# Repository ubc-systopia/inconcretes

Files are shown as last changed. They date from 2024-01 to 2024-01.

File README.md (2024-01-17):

<!-- # IVP System Guide -->

This repository contains source code and build documentation for a physical inverted pendulum test platform. The physical system, seen below, works to keep the pendulum shaft upright by actuating a pendulum cart along a track. To achieve this, we use a PID controller program that runs on a network of 4 Raspberry Pis. The Pis are able to communicate with each other using a distributed key value store. 

<p align = "center">
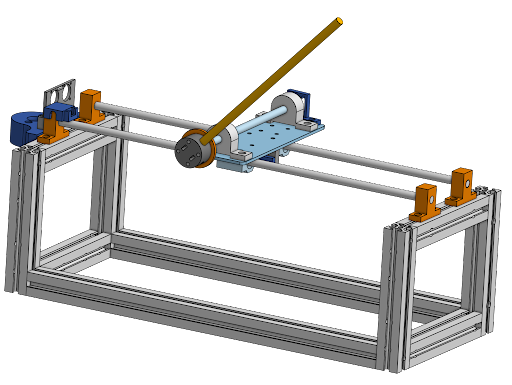
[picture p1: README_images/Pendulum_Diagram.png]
  
</p>

## Controls

### PID Control
<p align="center">
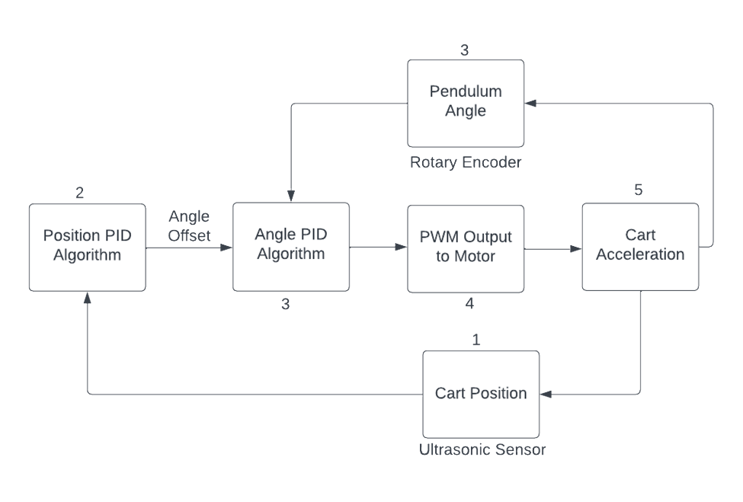
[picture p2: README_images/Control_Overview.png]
  
</p>

PID Control is used to actuate system and balance the pendulum. There are 2 PID algorithms running at different sampling rates (30 Hz for Position PID and 200 Hz for Angle PID were lower bounds in our testing). 

The PID algorithm tracks the error of a system over time and applies the following computation to it:

$$
  u(t)=K_pe(t)+ K_i \int_{a}^{b} e(\tau) \,d\tau + K_d \frac{d}{dt} e(t)
$$
<!-- <p align="center">
  <img src="README_images/PID_Equation.png" />
</p> -->
<!-- ![PID_Equation](README_images/PID_Equatvion.png) -->

The proportional term of $K_pe(t)$ can be thought of as **reacting immediately to the current error**, the integralterm as **accumulating past errors over time**, and the derivative as **predicting future error trends**. PID control offers a cost-effective and straightforward solution compared to more complex control methods. 

The position PID algorithm takes the Cart Position as an input. This is given by an ultrasonic sensors on the sides of the assembly, then filtered before being passed as an input. The position PID algorithm then computes an output which we call an Angle Offset. This is an offset to the real angle of the pendulum and works to amplify the response of the angle controller when the cart nears the edges of the track. Without this controller, the pendulum has no incentive to remain with the bounds of the track.

The angle controller takes the current angle of the pendulum along with the offset provided by the position controller and computes the appropriate signal to send to the motor accordingly. A larger deviation from the desired angle results in more force applied by the motor to correct the pendulum.

## System Overview

### Starting with a Single Node Setup

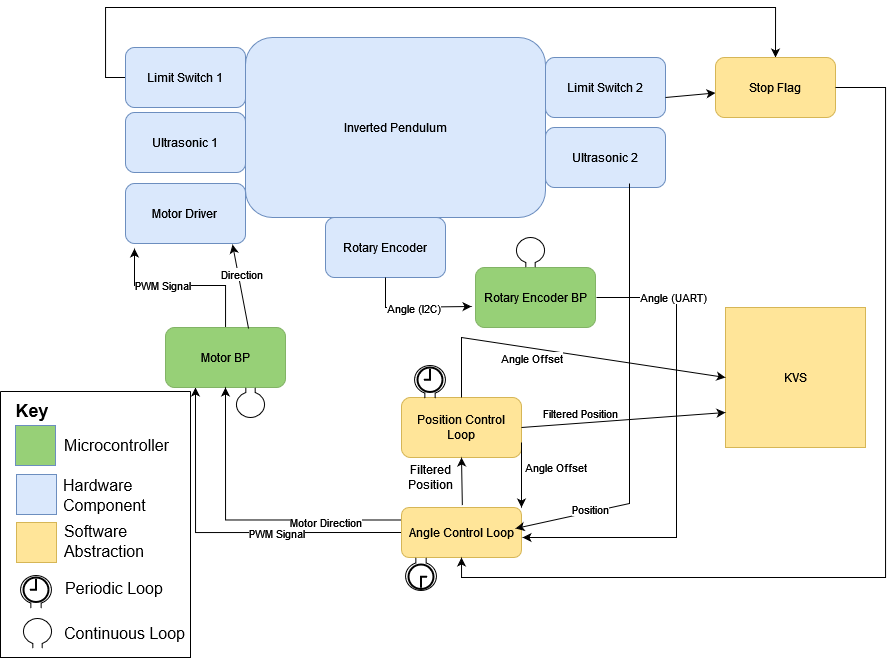
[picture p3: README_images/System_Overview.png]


A diagram for the system for a single node configuration is seen above.  

The physical build consists of the pendulum itself, with a Rotary Encoder, 2 Ultrasonic sensors, 2 limit switches and a motor driver. 

In order to control the pendulum we periodically drive the motor on the pendulum using a PWM signal, which is scaled and given direction based on the state of the system, using the PID scheme outlined above.

The single node in the setup is running 2 periodic tasks at different periods, a **Position Control Loop** and an **Angle Control Loop**. At the Position Control Loop we read a filtered position of the cart and use this as input to the Position PID algorithm. The output is saved to our Key Value Store and is shared with the Angle Control Loop through a shared memory location. 

The **Rotary Encoder BP** is a microcontroller running a continuous loop which reads the **Rotary Encoder** to find the current angle of the pendulum in every loop and forwards this value to the **Angle Control Loop**. The **Angle Control Loop** also receives a reading for the cart's current position along the track from **Ultrasonic 1**. 

 The **Angle Control Loop** performs some filtering of the position and shared this back to the Position Control Loop through a shared memory location. The **Angle Control Loop** uses the output of the position control loop for the angle PID algorithm to give us the output to the Pendulum. This output is in the form a scalar value that is then translated to the duty cycle and direction of a PWM signal.

The **Motor BP** is another microcontroller that is running a continuous loop where it receives the PWM signal from the **Angle Control Loop** and forwards it to the motor driver which then actuates the actual pendulum to achieve control. 

### Moving to a Multi Node Setup

<p align="center">
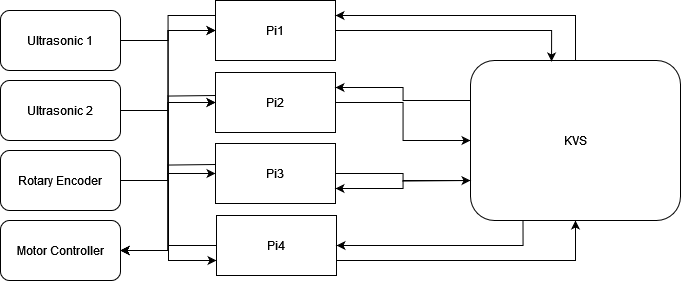
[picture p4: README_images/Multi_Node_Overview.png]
  
</p>
<!-- ![MultiNode.drawio(2).png](README_images/Multi_Node_Overview.png) -->

In a Multi Node Setup,, we have a maximum of 4 Raspberry Pi Nodes. Each of these is running an **Angle Control Loop** and a **Position Control Loop**. 2 Pis are capable of receiving position values from an independent Ultrasonic Sensor, and all 4 Pis are capable of receiving angular values from the **Rotary Encoder BP**. 

Position values can be shared across the Pis using the KVS, along with the control output from each Pi, along with any other values.

Each Pi computes its own control output, comprised of the PWM and Direction signals which are sent to the **Motor BP**. The **Motor BP** is then responsible for deciding on the output to send to the **Motor Driver**, which actuates the cart along the pendulum platform.

## Running on Raspberry Pis

We assume the following:
  - 4 raspberry pi nodes with hostnames `achal01-achal04`
  - nodes can access each other via SSH without passwords
  - this repository is cloned in the home directory of each node
  - PTP is installed
  
### PTP and VLAN config

Run `ifconfig`, expected output:

    eth0: flags=4163<UP,BROADCAST,RUNNING,MULTICAST>  mtu 1500
            inet 198.162.55.144  netmask 255.255.254.0  broadcast 198.162.55.255
            inet6 fe80::3a6:5deb:2c59:cd7f  prefixlen 64  scopeid 0x20<link>
            ether dc:a6:32:cd:ce:77  txqueuelen 1000  (Ethernet)
            RX packets 130046388  bytes 273546776 (260.8 MiB)
            RX errors 0  dropped 0  overruns 0  frame 0
            TX packets 131685298  bytes 406542628 (387.7 MiB)
            TX errors 0  dropped 0 overruns 0  carrier 0  collisions 0

    lo: flags=73<UP,LOOPBACK,RUNNING>  mtu 65536
            inet 127.0.0.1  netmask 255.0.0.0
            inet6 ::1  prefixlen 128  scopeid 0x10<host>
            loop  txqueuelen 1000  (Local Loopback)
            RX packets 76902811  bytes 8946060175 (8.3 GiB)
            RX errors 0  dropped 0  overruns 0  frame 0
            TX packets 76902811  bytes 8946060175 (8.3 GiB)
            TX errors 0  dropped 0 overruns 0  carrier 0  collisions 0

Run the following commands:
  ```bash
    sudo ip link add link eth0 name eth0.11 type vlan id 1 egress 0:2 1:2 2:2 3:2 4:2 5:2 6:2 7:2
    sudo ip link add link eth0 name eth0.12 type vlan id 2 egress 0:4 1:4 2:4 3:4 4:4 5:4 6:4 7:4
  ```
Again run `ifconfig`, expected output:
```
eth0: flags=4163<UP,BROADCAST,RUNNING,MULTICAST>  mtu 1500
        inet 198.162.55.144  netmask 255.255.254.0  broadcast 198.162.55.255
        inet6 fe80::3a6:5deb:2c59:cd7f  prefixlen 64  scopeid 0x20<link>
        ether dc:a6:32:cd:ce:77  txqueuelen 1000  (Ethernet)
        RX packets 130046461  bytes 273556620 (260.8 MiB)
        RX errors 0  dropped 0  overruns 0  frame 0
        TX packets 131685371  bytes 406551468 (387.7 MiB)
        TX errors 0  dropped 0 overruns 0  carrier 0  collisions 0

eth0.11: flags=4163<UP,BROADCAST,RUNNING,MULTICAST>  mtu 1500
        inet6 fe80::6584:daac:a387:87c4  prefixlen 64  scopeid 0x20<link>
        ether dc:a6:32:cd:ce:77  txqueuelen 1000  (Ethernet)
        RX packets 0  bytes 0 (0.0 B)
        RX errors 0  dropped 0  overruns 0  frame 0
        TX packets 4  bytes 686 (686.0 B)
        TX errors 0  dropped 0 overruns 0  carrier 0  collisions 0

eth0.12: flags=4163<UP,BROADCAST,RUNNING,MULTICAST>  mtu 1500
        inet6 fe80::824d:a435:2f9b:ca3a  prefixlen 64  scopeid 0x20<link>
        ether dc:a6:32:cd:ce:77  txqueuelen 1000  (Ethernet)
        RX packets 0  bytes 0 (0.0 B)
        RX errors 0  dropped 0  overruns 0  frame 0
        TX packets 7  bytes 976 (976.0 B)
        TX errors 0  dropped 0 overruns 0  carrier 0  collisions 0

lo: flags=73<UP,LOOPBACK,RUNNING>  mtu 65536
        inet 127.0.0.1  netmask 255.0.0.0
        inet6 ::1  prefixlen 128  scopeid 0x10<host>
        loop  txqueuelen 1000  (Local Loopback)
        RX packets 76902811  bytes 8946060175 (8.3 GiB)
        RX errors 0  dropped 0  overruns 0  frame 0
        TX packets 76902811  bytes 8946060175 (8.3 GiB)
        TX errors 0  dropped 0 overruns 0  carrier 0  collisions 0
```
Check the PTP status using systemctl status ptp4l and find the path of the ptp4l service

For example, the output will contain a line `Loaded: loaded ( ; enabled; vendor preset: enabled)`

Open file using  `sudo vim /lib/systemd/system/ptp4l.service` and check the ethernet interface used by PTP

By default, it is `eth0`, replace it with `eth0.11`

Run the following systemctl commands:
  ```bash
  sudo systemctl daemon-reload
  sudo systemctl restart ptp4l
  ```

### Running the Pendulum
<!-- 1. Run [`setup.sh`](http://setup.sh) on each Pi -->
1. Naviagate to this repository on Pi 1
2. Build the project:
    1. Navigate to the `build` directory
    2. run `cmake ..`
    3. run `make`
3. Enable UART on each of the Pis from the `raspi config` tool.
4. Callibrate pendulum by running the following command in the build directory of any of the connected Pis:
    ``` bash
    sudo ./test_AS5600
    ```
    This displays the rotary encoder angle, balance the pendulum manually and note the encoder value shown in the terminal. Ideally, this should be 2000 plus or minus 300, to keep the rollover state for angle outside the operating range of the pendulum.

5. Run the pendulum application from the project directory:

    ```bash
    sudo ./pivp_run.sh $NUM_NODES $POSITION_LOOP_PERIOD $ANGLE_LOOP_PERIOD $POSITION_KP $POSITION_KD $POSITION_KI $ANGLE_KP $ANGLE_KD $ANGLE_KI $POSITION_SET_POINT $ANGLE_SET_POINT
    ```

      Values that worked well for our system for the other parameters:

      | Parameter | Value |
      |--- | --- |
      |`NUM_NODES`| number of nodes you are running with| 
      | `POSITION_LOOP_PERIOD`: | 20 |
      | `ANGLE_LOOP_PERIOD`: | 6 |
      | `POSITION_KP`: | 0.01 |
      | `POSITION_KD`: | 0.08 |
      | `POSITION_KI`: | 0 |
      | `ANGLE_KP`: | 25 |
      | `ANGLE_KD`: | 2.5 |
      | `ANGLE_KI`: | 150 |
      | `POSITION_SET_POINT`: | 20 - Corresponds to distance from side to middle of track in cm |
      | `ANGLE_SET_POINT`: | calibration value from previous step |

6. Press either limit switch on sides of pendulum track to stop a run of the pendulum
7. Logs for the run are available at local nodes at ‘PiCtlLogs/date-of-runcompletion_time-of-completion_PiN’

## Pendulum Build Documentation
Detailled descriptions of how to build the pendulum and various aspects of the systemn are included in subdirectories of this project.
- [`Bluepill_Firmware`](Bluepill_Firmware): Firmware for 2 Bluepill microcontrollers used, along with instructions for how to flash the firmware on the devices.
- [`PCB_Designs_Docs`](PCB_Designs_Docs): All PCB design files for the custom PCBs used in the pendulum, including labelled circuit diagrams for reference, gerber and drill files for fabrication. Additionally, all electrical components and quantities, with purchase links are shown. 
- [`Mech_Docs`](Mech_Docs): All mechanical components with purchase links and quantities are included. Additionally, CAD design files, STL files for 3D printed parts and DXFs for laser cut parts are included.

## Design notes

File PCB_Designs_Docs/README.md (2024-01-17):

# Inverted Pendulum Electrical Documentation and PCB Designs

## Components/Sensors Used

| Component | Quantity | Purchase Link | Notes |
| --- | --- | --- | --- |
| Ultrasonic Sensor | 2 | https://www.digikey.ca/short/wqjn48db |  |
| AS5600 Rotary Encoder | 1 | https://a.co/d/2jkT8j0 | Prebuilt breakout board with magnet included used |
| Brushed DC Motor | 1 | https://a.co/d/41Gn3cl | Any smooth motion motor with low cogging and similar specifications is usable. |
| Raspberry Pi 4B | 4 | -  | - |
| Bluepill (STM32F103C dev board) | 2 | https://a.co/d/aVWNCsf |  |
| ST-Link V2 | 1 | https://a.co/d/aVWNCsf |  |
| 12 V Motor Driver | 1 | https://www.cytron.io/p-10amp-5v-30v-dc-motor-driver |  |
| 12 V Power Supply | 1 | https://www.digikey.ca/short/t58bfrvt |  |
|  4.7 kOhm Resistor | 2 | https://www.digikey.ca/short/v238crf2 | For I2C Lines |
| JST Connector Set | 1 | https://a.co/d/0fB4Xf2 |  |
| I2C OLED Display Module | 2 | https://a.co/d/eMWrLmH |  |
| Header Pins (Male) | 8 | https://www.digikey.ca/short/54wwz4hv |  |
| Header Pins (Female) | 4 | https://www.digikey.ca/short/5cdf2dd4 |  |
| Custom PCBs | 4 | Download design files and manufacture at any PCB fab. | Details included below in PCB Design Section |
| PJ002A Connector | 1 | https://www.digikey.ca/short/v80h319m |  |
| AC DC Wall Power Adapter, Barrel Jack | 1 | https://www.digikey.ca/short/rw25c3v4 |  |
| Limit Switch | 2 | https://www.digikey.ca/short/8dmrj95d |  |

## PCB Design

In testing and integration of the system, I found that wiring using Dupont (jumper) wires to connect to the Pi headers was not a suitable long term solution as sensors would come unplugged and connections were unreliable. 

I elected to instead design a few custom Pi Hat PCBs that could plug into the Raspberry Pi 4Bs GPIO Headers. These PCBs included JST connectors for more permanent connections to sensors and allowed for cleaner, reliable wiring. To keep connections clean, zip ties and cable tie mounts were used to bundle and route wires.

Below are descriptions for the KiCad projects used to manufacture the PCBs for the project, as well as labelled diagrams of the PCB for an end user.

### **PCB Files**

Pi Hat (`Pi1_PiHat`):

This is the Pi Hat for the “main” Raspberry Pi. In a single node setup, this PCB alone with 1 Raspberry PI is sufficient. 

<p align="center">
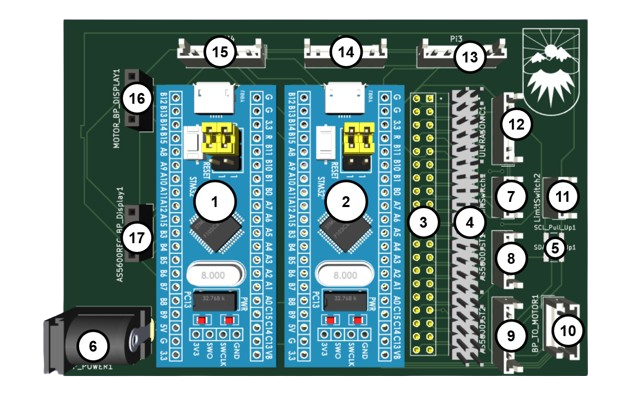
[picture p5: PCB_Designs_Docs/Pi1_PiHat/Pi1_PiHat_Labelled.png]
  
</p>

<!-- ![Pi1_PiHat_Labelled.png](./Pi1_PiHat/Pi1_PiHat_Labelled.png) -->

| Number | Label | Description |
| --- | --- | --- |
| 1 | AS5600 Distributor Bluepill | BP responsible for receiving AS5600 communication over I2C and sending this over UART to all connected Pis |
| 2 | PWM Forwarder Bluepill | BP responsible for receiving the PWM signal from all Pi’s and sending the final output PWM signal to the motor |
| 3 | Board to Pi Header | Connects to 40 pin Pi Header |
| 4 | Pi Header Extension | Allows access to all Pi Header pins |
| 5 | I2C Pullup Resistors |  |
| 6 | Barrel Jack (PJ002A) | 3V3 Power Input for Bluepills |
| 7 | Limit Switch 1 Connector | Limit switch input, allows detection for when cart is at rails of the physical track |
| 8 | AS5600 Connector 1 | Connector for I2C comms, direction signal and programming pins of AS5600 |
| 9 | AS5600 Connector 2 | Connector for power, ground and analog output of AS5600 |
| 10 | BP to Motor Connector | Connection to share ground, send direction and PWM to the motor driver |
| 11 | Limit Switch 2 Connector | Limit switch input, allows detection for when cart is at rails of the physical track |
| 12 | Ultrasonic 1 Connector |  |
| 13 | Pi1 to Pi3 Connector | Connects ground, AS5600 Distributor BP UART Tx line, limit switches and motor instruction lines |
| 14 | Pi1 to Pi2 Connector | Connects ground, AS5600 Distributor BP UART Tx line, limit switches and motor instruction lines |
| 15 | Pi1 to Pi4 Connector | Connects ground, AS5600 Distributor BP UART Tx line, limit switches and motor instruction lines |
| 16 | PWM Forwarder BP to Display Connector | Connector for BP to digital display |
| 17 | AS5600 Distributor BP to Display Connector | Connector for BP to digital display |

Pi Hat 2 (`Pi2_PiHat`):

This is the Pi Hat for the secondary node for a simple two node setup. The second node has a connector to the “main” Pi Hat as well as an additional Ultrasonic sensor.

<p align="center">
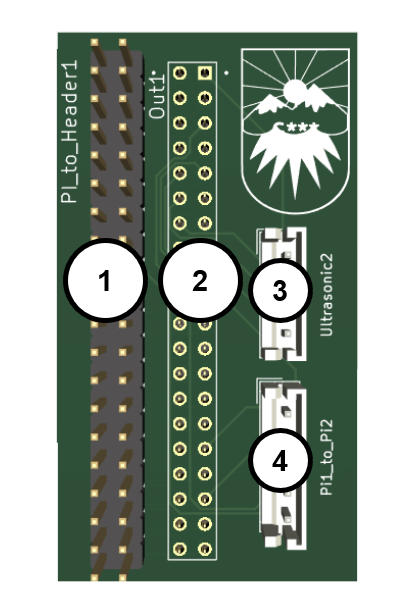
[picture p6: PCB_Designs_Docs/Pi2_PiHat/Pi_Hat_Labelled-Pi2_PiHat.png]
  
</p>

| Number | Label | Description |
| --- | --- | --- |
| 1 | Board to Pi Header | Connects to 40 pin Pi Header |
| 2 | Pi Header Extension | Allows access to all Pi Header pins |
| 3 | Ultrasonic 2 Connector |  |
| 4 | Pi1 to Pi2 Connector | Connects ground, AS5600 Distributor BP UART Tx line, limit switches and motor instruction lines |

Pi Hat N (`PiN_PiHat`):
<p align="center">
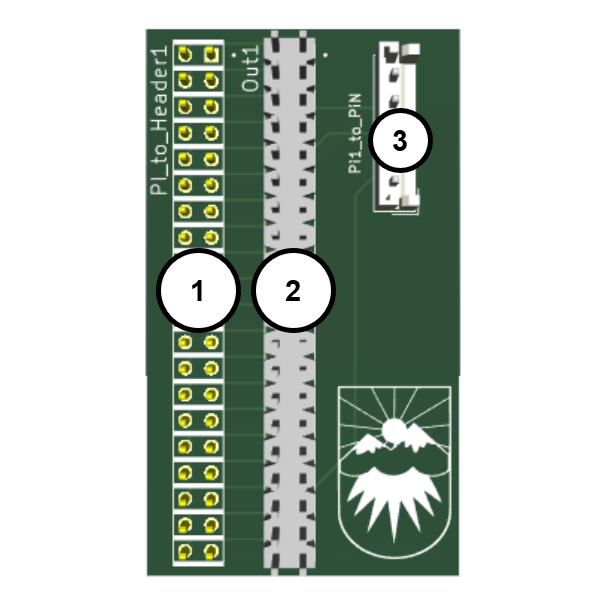
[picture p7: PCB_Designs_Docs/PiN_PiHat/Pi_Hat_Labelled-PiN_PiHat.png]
  
</p>

| Number | Label | Description |
| --- | --- | --- |
| 1 | Board to Pi Header | Connects to 40 pin Pi Header |
| 2 | Pi Header Extension | Allows access to all Pi Header pins |
| 4 | Pi1 to PiN Connector | Connects ground, AS5600 Distributor BP UART Tx line, limit switches and motor instruction lines |

This is the Pi Hat for all additional nodes. It includes a connector to the main Pi Hat to share ground, a UART line, limit switch input, and outputs to the motor driving Bluepill.

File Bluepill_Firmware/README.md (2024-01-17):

# Inverted Pendulum Firmware

### Microcontroller Firmware

The microcontroller chosen for this project was the STM32F103C, commonly use as part of the dev board known as the Bluepill:

<!-- ![Untitled](README_images/Bluepill.jpeg) -->
<p align="center">
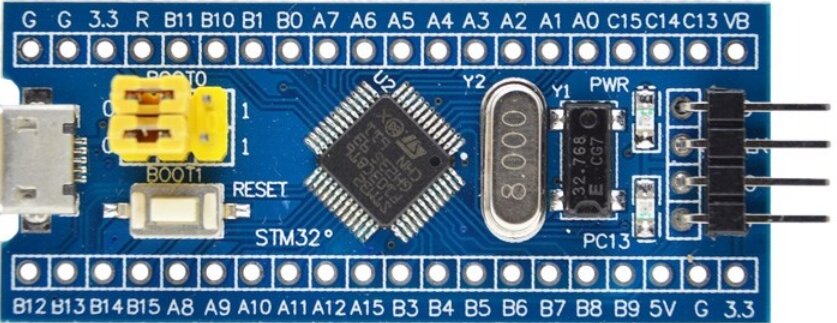
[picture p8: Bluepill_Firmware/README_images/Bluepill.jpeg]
  
</p>

To allow the Raspberry Pi nodes for the Inverted Pendulum to act as replicas in a distributed system, we did not want to have leader nodes. In order to actuate the motor for the pendulum, we need a single input to a motor driver circuit in the form of a PWM signal. So, we elected to use an intermediate microcontroller which is responsible for receiving the output in the form of a PWM signal from all of the Raspberry Pi nodes, and then output a final PWM signal to the motor driver.

<p align="center">
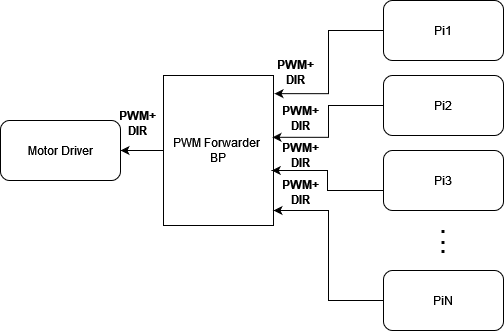
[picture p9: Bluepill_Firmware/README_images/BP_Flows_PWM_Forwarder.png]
  
</p>
<!-- ![BP_Flows_PWM_Forwarder.png](README_images/BP_Flows-PWM_Forwarder.png) -->

A second Bluepill is used to distribute the rotary encoder output to the Raspberry Pi nodes. This Bluepill acts as an I2C master to the AS5600 I2C minion rotary encoder. The received angle is then sent to the raspberry pi nodes over UART as the Raspberry Pi 4B used for this project does not have the necessary hardware to be used as an I2C minion. 

<p align="center">
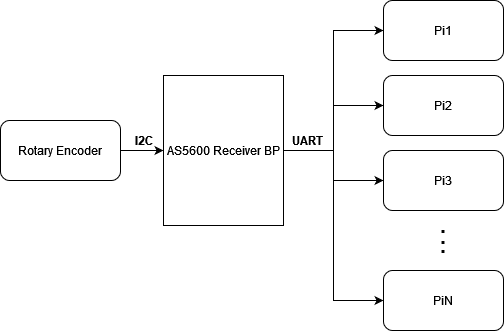
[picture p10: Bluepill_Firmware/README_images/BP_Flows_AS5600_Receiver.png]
  
</p>
<!-- ![BluepillFlows.drawio.png](README_images/BP_Flows_AS5600_Receiver.png) -->

For ease of development and flashing, we elected to use PlatformIO with the Arduino framework for the firmware on the microcontrollers. PlatformIO is an open-source ecosystem for embedded development that provides a unified development platform for multiple microcontroller architecture. If you use VSCode, you can install the [PlatformIO extension](https://marketplace.visualstudio.com/items?itemName=platformio.platformio-ide). Otherwise, please install the CLI version, following these instructions:

[https://docs.platformio.org/en/latest/core/installation/index.html](https://docs.platformio.org/en/latest/core/installation/index.html).

The following instructions outline how to flash the Bluepill microcontrollers assuming that you are using the CLI:

Connect to the PWM forwarder Bluepill using an ST-Link V2 programmer. Navigate to ‘BluepillFirmware/PWMForwarder’ in your terminal and run:

```bash
pio run --target upload
```

If flashing is successful and there is no PWM output any connected Pis, the digital display connected to the PWM Forwarder will display “”.

Now, you can connect the ST-Link to the AS5600 Bluepill, navigate to the ‘BluepillFirmware/AS5600ReceiverBP’ folder and run

```bash
pio run --target upload
```

If flashing is successful, and the connection to the sensor is live, then the connected digital display will read “Hello World”.

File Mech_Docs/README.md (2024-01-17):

# Inverted Pendulum Mechanical Design and Build Notes

## Components Used

********Basic components such as nuts, bolts, washers and spacers are not included********

### Pendulum Frame

| Item | Quantity | Link | Specifications |
| --- | --- | --- | --- |
| T-Slot Nuts | 32 | https://www.mcmaster.com/products/t-slot-nuts/t-slotted-framing-fasteners-4/system-of-measurement~metric/rail-height~20mm/ | Single Nut, 20 mm single rail height |
| Corner Brackets | 8 | https://www.mcmaster.com/products/corner-brackets/t-slotted-framing-structural-brackets/ | 20 mm rail height |
| Aluminum T-Slot Framing Rails | 8 | https://www.mcmaster.com/products/aluminum-extrusions/rail-profile~single/single-rail-profile-style~four-slot/system-of-measurement~metric/rail-height~20mm/rail-widt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 | 0.5ft length, 20 mm rail height |
| Aluminum T-Slot Framing Rails | 2 | https://www.mcmaster.com/products/aluminum-extrusions/rail-profile~single/single-rail-profile-style~four-slot/system-of-measurement~metric/rail-height~20mm/rail-widt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 | 1.5 ft length, 20 mm rail height |

### Linear Motion System

| Item | Quantity | Link | Specifications |
| --- | --- | --- | --- |
| Linear Motion Shaft | 2 | https://www.mcmaster.com/products/linear-shafts/linear-motion-shafts-5/system-of-measurement~metric/diameter~8mm/length~600-mm/ | Shaft Length: 8 mm, Shaft Diameter: 600 mm |
| Shaft Collars | 4 | https://www.amazon.ca/Aluminum-Linear-Support-Motion-Diameter/dp/B08JTPG54L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,aps,131&sr=8-2 | Bore Diameter: 8 mm  |
| Linear Ball Bearings | 2 |  | Bore Diameter: 8 mm |
| GT2 Idler | 1 | https://a.co/d/6dsKSIS | Tooth Profile: GT2 |
| GT2 Motor Mounted Pulley | 1 | https://a.co/d/6dsKSIS | Tooth Profile: GT2, Bore Diameter:  |
| Timing Belt | 1 | https://a.co/d/6dsKSIS | Tooth Profile: GT2, Bore Diameter:  |
| Clamp Mount Block | 1 | https://a.co/d/6dsKSIS | Tooth Profile: GT2 |
| Motor Mount | 1 | 3D Print STL: [`Motor_Mount.stl`](Motor_Mount.stl) | Material: PLA, Dimensions: |
| Cart Timing Belt Mount | 1 | 3D Print STL: [Cart_Timing_Belt_Mount.stl](Cart_Timing_Belt_Mount.stl) | Material: PLA, Dimensions: |
| Idler Mount | 1 | 3D Print STL: [`Idler_Mount.stl`](Idler_Mount.stl)  | Material: PLA, Dimensions: |
| Motor Driver Mount | 1 | Laser Cutter DXF: [`Motor_Driver_Mount.stl`](Motor_Driver_Mount.stl) | Material: MDF, Dimensions: |

### **Pendulum Shaft System**

| Item | Quantity | Link | Specifications |
| --- | --- | --- | --- |
| Pendulum to Rotary Shaft Mount | 1 | 3D Print STL: [`Pendulum_To_Rotary_Shaft_Mount.stl`](Pendulum_To_Rotary_Shaft_Mount.stl) | Material: PLA, Dimensions:  |
| Rotary Shaft Flange | 1 | https://a.co/d/g265dLN | Bore Diameter: 10 mm |
| Rotary Mounted Bearings | 1 | https://a.co/d/airvwwv | Bore Diameter: 10 mm |
| Rotary Shaft | 1 | https://www.mcmaster.com/products/rotary-shafts/rotary-shafts-5/system-of-measurement~metric/ | Diameter: 10 mm, Length: 200 mm, Material: 1566 Carbon Steel |
| AS5600 Mount | 1 | 3D Print STL: [`AS5600_Mount.stl`](AS5600_Mount.stl) | Material: PLA, Dimensions:  |
| Pendulum Cart | 1 | Laser Cutter DXF: [`Pendulum_Cart.dxf`](Pendulum_Cart.dxf) | Material: MDF, Dimensions |
|  |  |  |  |

### **Sensor Mounts**

| Item | Quantity | Link | Specifications |
| --- | --- | --- | --- |
| Motor-Side Ultrasonic Mount | 1 | 3D Print STL: [`Ultrasonic_Mount.stl`](Ultrasonic_Mount.stl) | Material: PLA, Dimensions: |
| Idler-Side Ultrasonic Mount | 1 | 3D Print STL: [`TODO`]() | Material: PLA, Dimensions: |
| Limit Switch Mount | 1 | 3D Print STL: [`Limit_Switch_Mount.stl`](Limit_Switch_Mount.stl) | Material: PLA, Dimensions: |
| Ultrasonic Reflection Surface | 1 | Laser Cutter DXF: [`TODO`]() | Material: Cardboard, Dimensions: |

### CAD Files

**Full Assembly**

[Onshape](https://cad.onshape.com/documents/4bf8413ba8de0c065cd15fe9/w/5f5a90b8a1e2c8779d00a033/e/c47179ad8bca38d01a648ef1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)

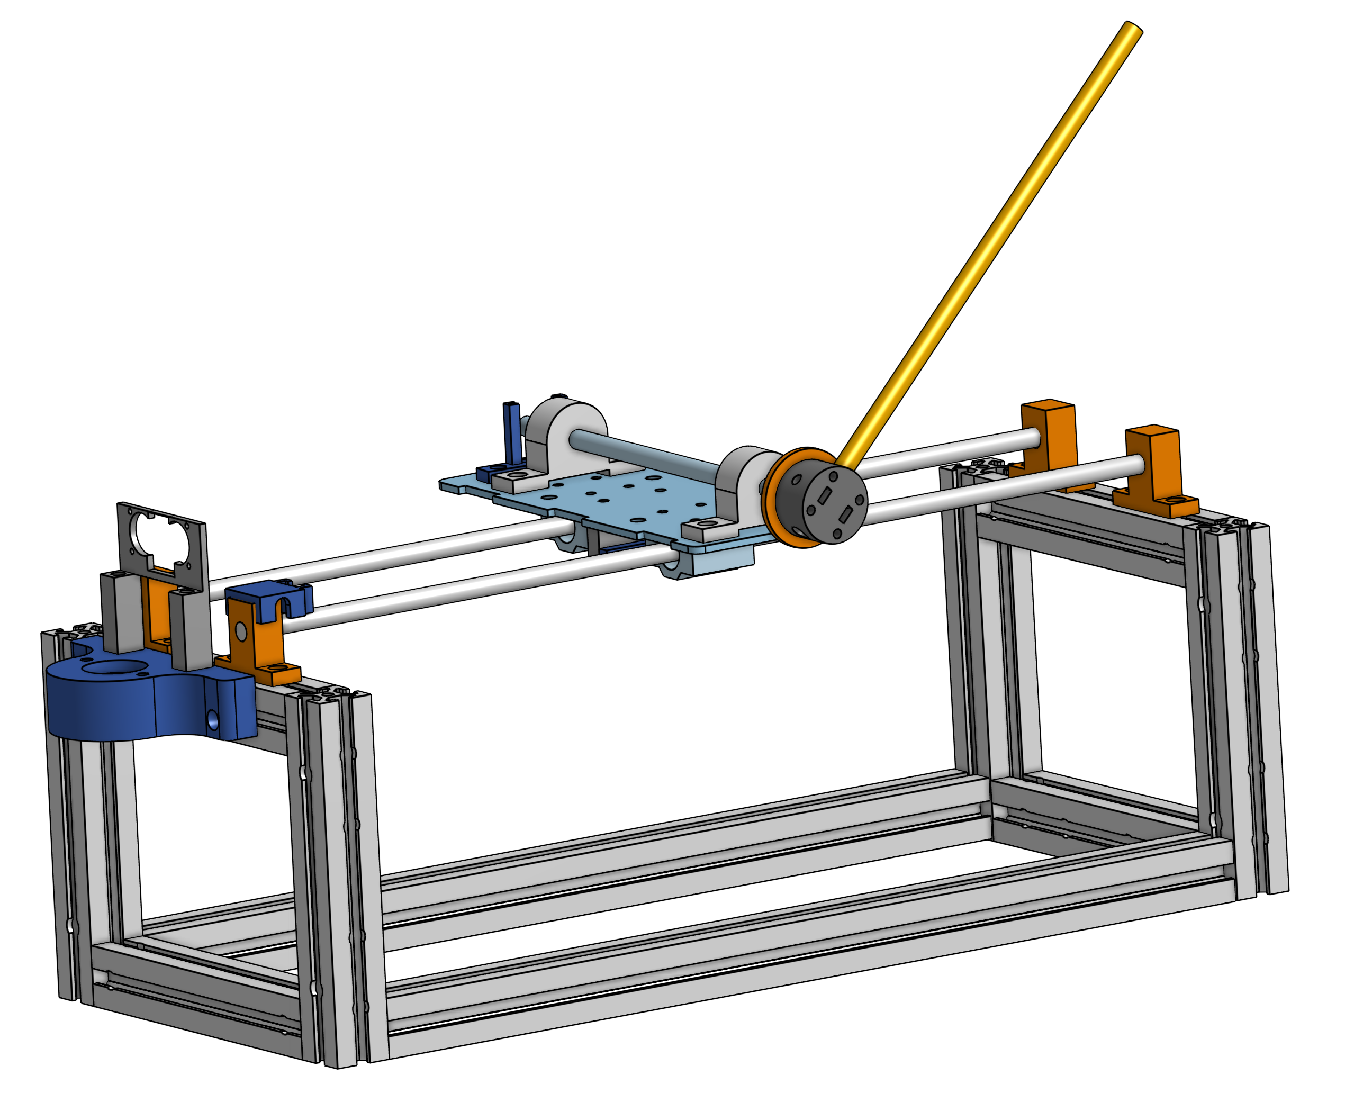
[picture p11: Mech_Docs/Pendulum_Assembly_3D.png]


### Mechanical Build Notes

- Alignment of the linear motion system is a key consideration during construction. Assembly should be completed on a strong, stable and level surface. Movement of the cart along linear motion rails should not cause binding towards the ends of the track, so adjust shaft collar positions along the t-slots as required for smooth motion and aligned linear motion shafts. Smooth motion of this system is important as jolts/jerkiness of the system causes unneeded difficulty in control of the unstable system and misalignments causes reliability concerns.
- Timing Belt should be under appropriate tension, you should be able to “strum” it, like a tight guitar string and it should not hang slack. Tension should be comparable to 3D printer timing belts.
- With the cart in constant motion with changing directions and vibrations in the system, it’s advisable to tighten bolts and add a second locking bolt. Alternatively, components such as loc-tite or locking nuts can be used to reduce the likelihood of vibrations causing nuts to fall.
- The linked aluminium extrusions available on McMaster-Carr have a non-standard footprint (i.e. not the commonly available 80x20 footprint). I would recommend using 8020 extrusions instead as it is easier to find parts to work with these extrusions (i.e. corner gussets, slot nuts, etc.) as you are not limited by what is available on McMaster-Carr. This may also result in a cheaper build.

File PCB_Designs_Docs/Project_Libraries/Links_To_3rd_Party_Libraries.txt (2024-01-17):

20x2 pin male header: https://www.snapeda.com/parts/7-146256-0/TE%20Connectivity/view-part/
Resistors: https://www.snapeda.com/parts/RC1206JR-130RL/Yageo/view-part/
Barrel Jack Power Connector: https://www.snapeda.com/parts/PJ-002A/CUI+Devices/view-part/
20x2 pin female header: https://www.snapeda.com/parts/SSQ-120-01-L-D/Samtec/view-part/

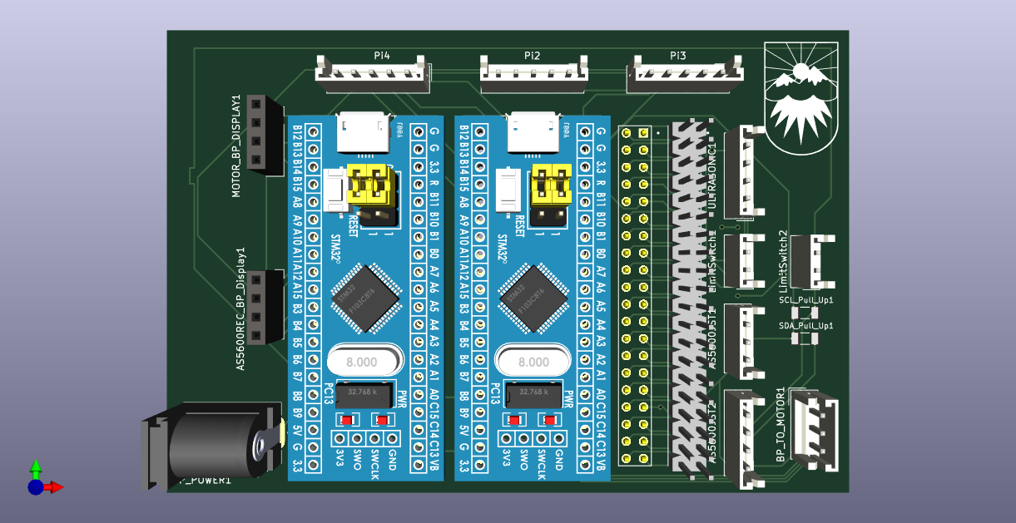
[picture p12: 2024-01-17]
PCB_Designs_Docs/Pi1_PiHat/Pi1_PiHat.png

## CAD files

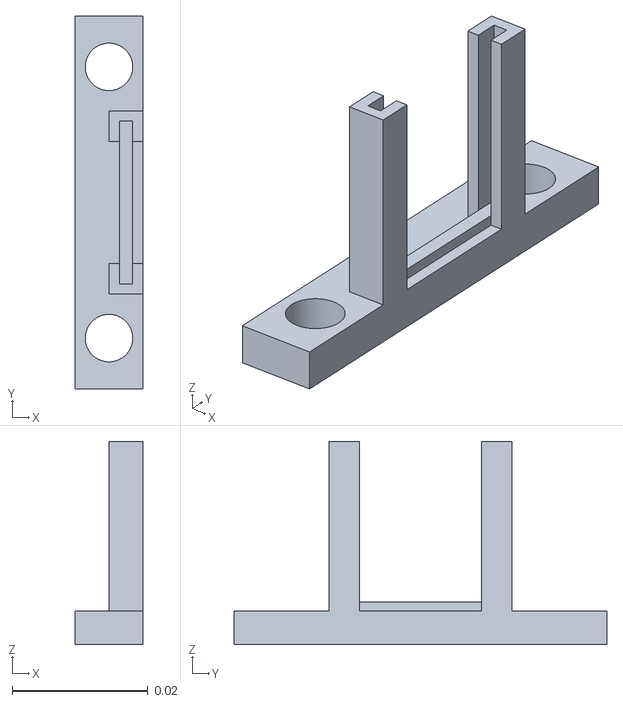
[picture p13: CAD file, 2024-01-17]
Mech_Docs/AS5600_Mount.stl
0.01 x 0.055 x 0.03

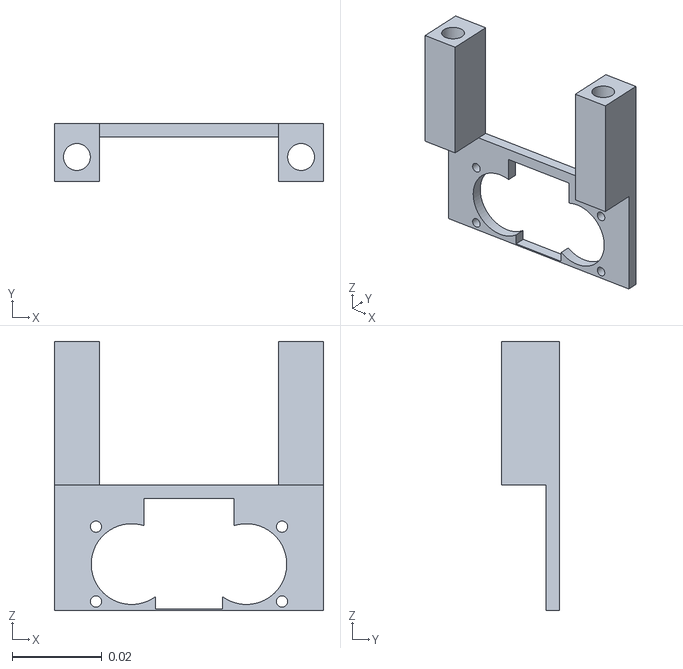
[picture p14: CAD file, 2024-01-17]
Mech_Docs/Ultrasonic_Mount.stl
0.06 x 0.013 x 0.06

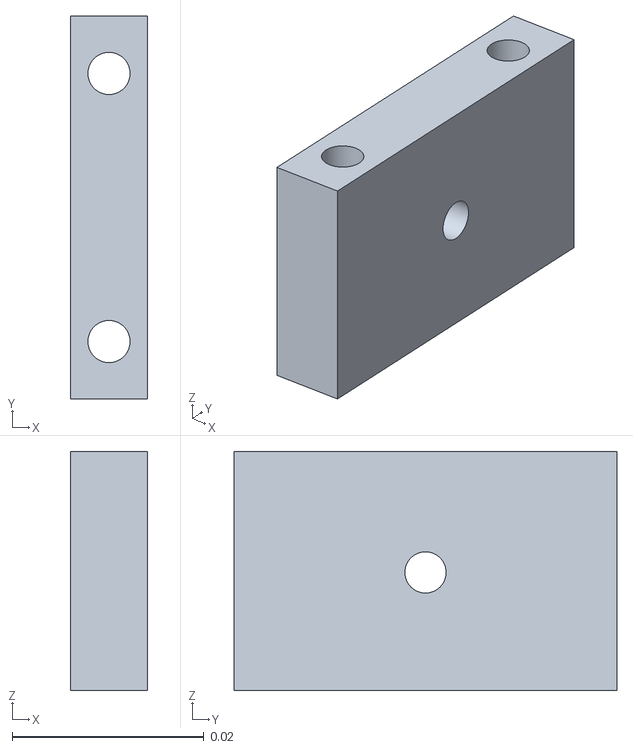
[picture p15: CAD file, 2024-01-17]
Mech_Docs/Cart_Timing_Belt_Mount.stl
0.008 x 0.04 x 0.025

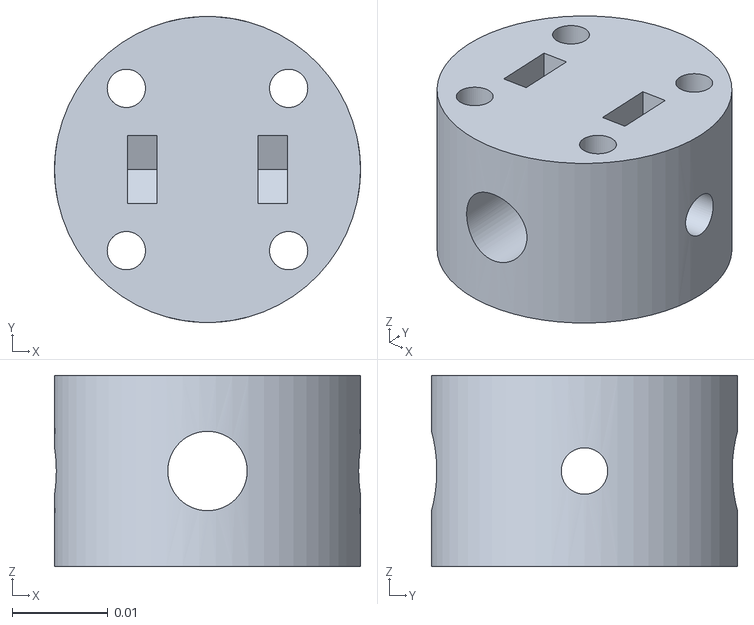
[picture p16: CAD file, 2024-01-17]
Mech_Docs/Pendulum_To_Rotary_Shaft_Mount.stl
0.032 x 0.032 x 0.02

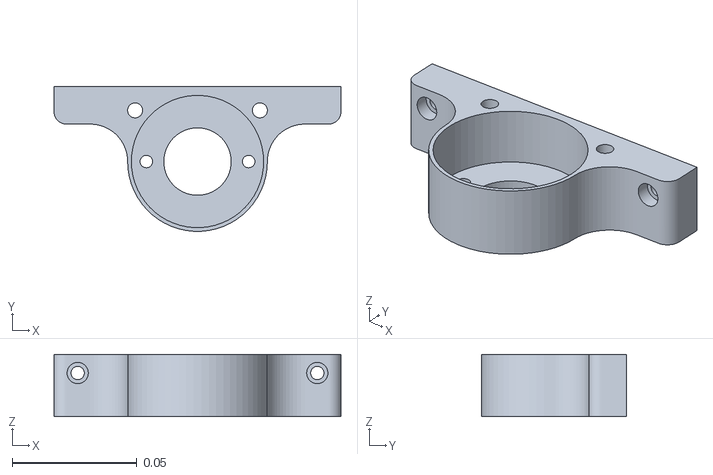
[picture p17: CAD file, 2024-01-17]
Mech_Docs/Motor_Mount.stl
0.115 x 0.058 x 0.025

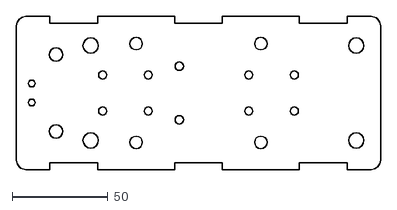
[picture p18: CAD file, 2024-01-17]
Mech_Docs/Pendulum_Cart.dxf
190.0 x 80.0

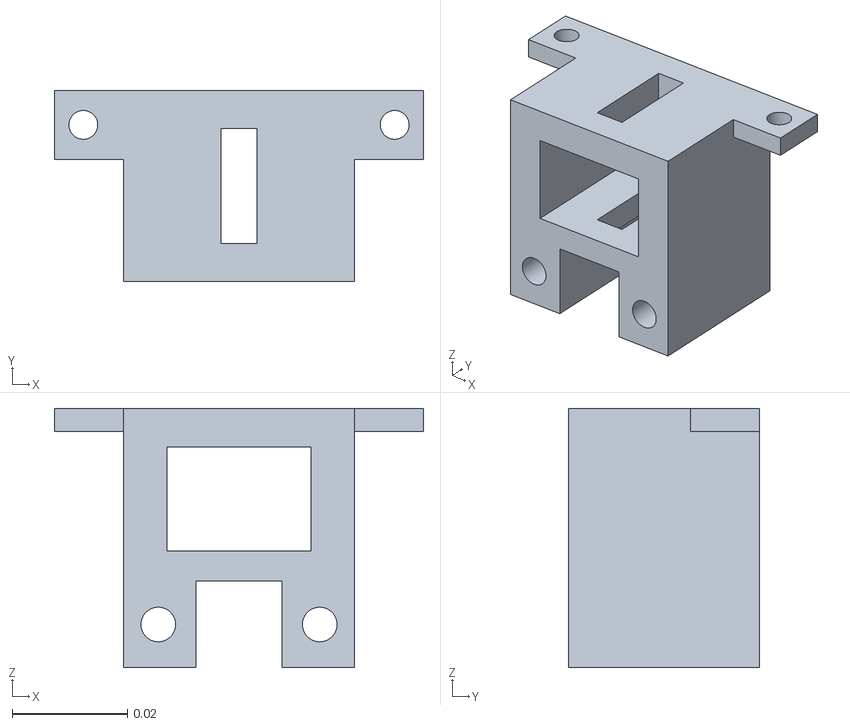
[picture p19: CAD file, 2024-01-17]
Mech_Docs/Idler_Mount.stl
0.064 x 0.0332 x 0.045

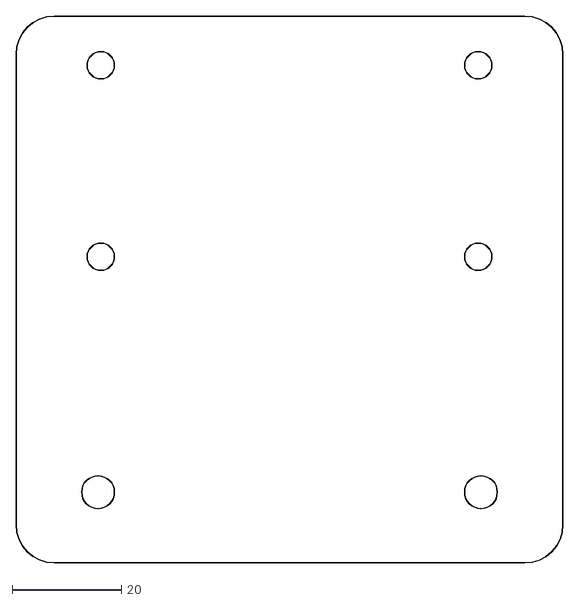
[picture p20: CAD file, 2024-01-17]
Mech_Docs/Motor_Driver_Mount.dxf
100.0 x 100.0

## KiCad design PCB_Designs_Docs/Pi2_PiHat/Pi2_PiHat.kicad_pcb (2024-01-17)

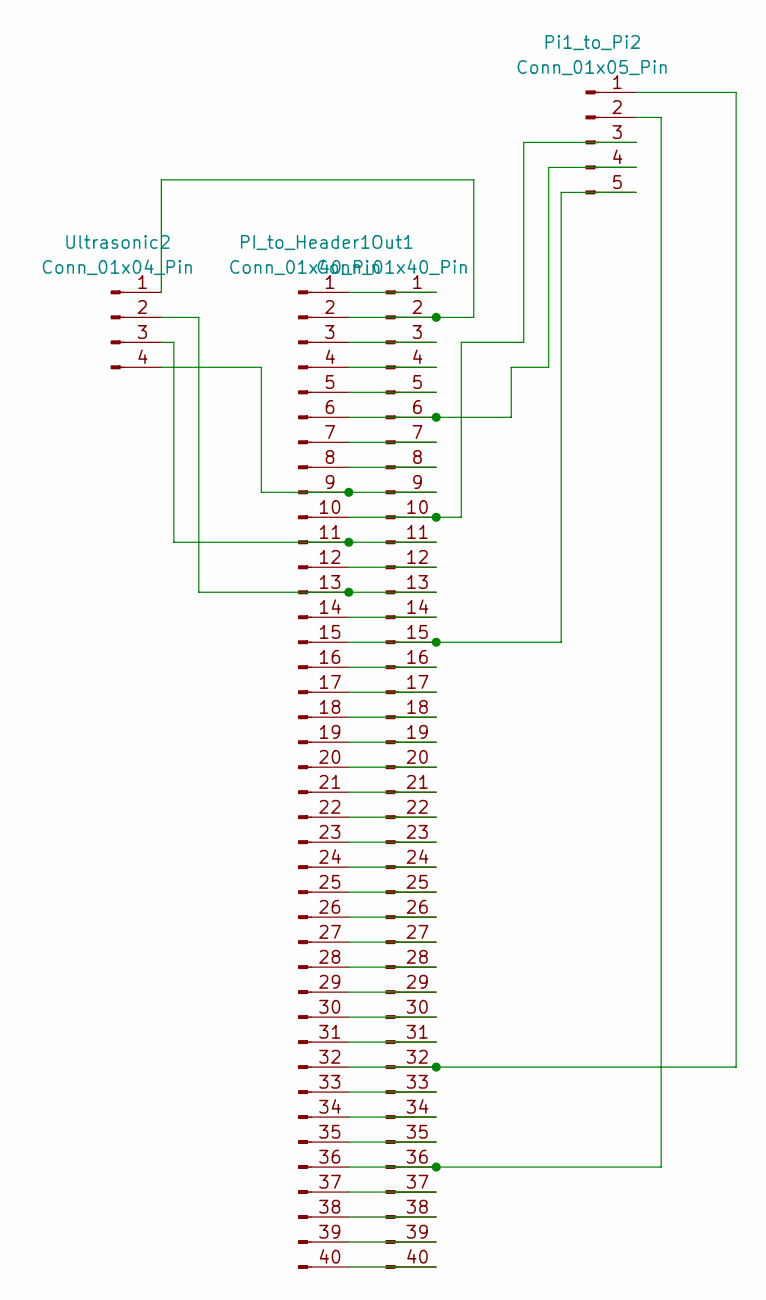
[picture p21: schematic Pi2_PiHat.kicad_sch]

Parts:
Out1: Conn_01x40_Pin; TE_7-146256-0
PI_to_Header1: Conn_01x40_Pin; TE_7-146256-0
Pi1_to_Pi2: Conn_01x05_Pin; JST_EH_B5B-EH-A_1x05_P2.50mm_Vertical
Ultrasonic2: Conn_01x04_Pin; JST_EH_B4B-EH-A_1x04_P2.50mm_Vertical

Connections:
unnamed: Out1.1, PI_to_Header1.1
unnamed: Out1.2, PI_to_Header1.2, Ultrasonic2.1
unnamed: Out1.3, PI_to_Header1.3
unnamed: Out1.4, PI_to_Header1.4
unnamed: Out1.5, PI_to_Header1.5
unnamed: Out1.6, PI_to_Header1.6, Pi1_to_Pi2.4
unnamed: Out1.7, PI_to_Header1.7
unnamed: Out1.8, PI_to_Header1.8
unnamed: Out1.9, PI_to_Header1.9, Ultrasonic2.4
unnamed: Out1.10, PI_to_Header1.10, Pi1_to_Pi2.3
unnamed: Out1.11, PI_to_Header1.11, Ultrasonic2.3
unnamed: Out1.12, PI_to_Header1.12
unnamed: Out1.13, PI_to_Header1.13, Ultrasonic2.2
unnamed: Out1.14, PI_to_Header1.14
unnamed: Out1.15, PI_to_Header1.15, Pi1_to_Pi2.5
unnamed: Out1.16, PI_to_Header1.16
unnamed: Out1.17, PI_to_Header1.17
unnamed: Out1.18, PI_to_Header1.18
unnamed: Out1.19, PI_to_Header1.19
unnamed: Out1.20, PI_to_Header1.20
unnamed: Out1.21, PI_to_Header1.21
unnamed: Out1.22, PI_to_Header1.22
unnamed: Out1.23, PI_to_Header1.23
unnamed: Out1.24, PI_to_Header1.24
unnamed: Out1.25, PI_to_Header1.25
unnamed: Out1.26, PI_to_Header1.26
unnamed: Out1.27, PI_to_Header1.27
unnamed: Out1.28, PI_to_Header1.28
unnamed: Out1.29, PI_to_Header1.29
unnamed: Out1.30, PI_to_Header1.30
unnamed: Out1.31, PI_to_Header1.31
unnamed: Out1.32, PI_to_Header1.32, Pi1_to_Pi2.1
unnamed: Out1.33, PI_to_Header1.33
unnamed: Out1.34, PI_to_Header1.34
unnamed: Out1.35, PI_to_Header1.35
unnamed: Out1.36, PI_to_Header1.36, Pi1_to_Pi2.2
unnamed: Out1.37, PI_to_Header1.37
unnamed: Out1.38, PI_to_Header1.38
unnamed: Out1.39, PI_to_Header1.39
unnamed: Out1.40, PI_to_Header1.40

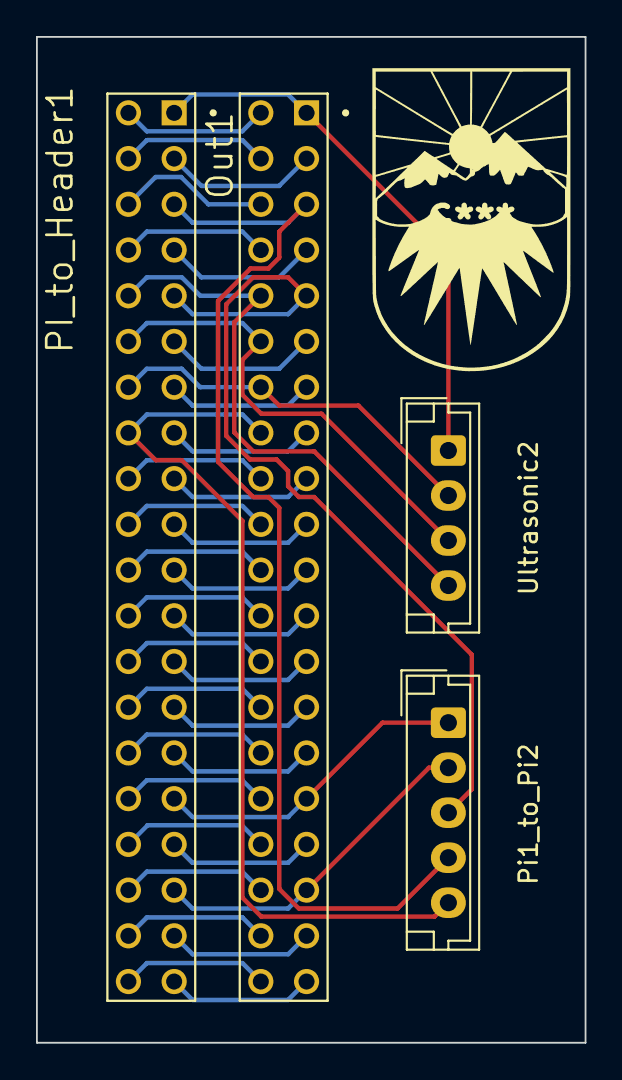
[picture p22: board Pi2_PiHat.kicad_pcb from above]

Board: 2 copper layers, 30.5 x 55.9 mm, 4 parts (0 on the bottom side), 40 nets.

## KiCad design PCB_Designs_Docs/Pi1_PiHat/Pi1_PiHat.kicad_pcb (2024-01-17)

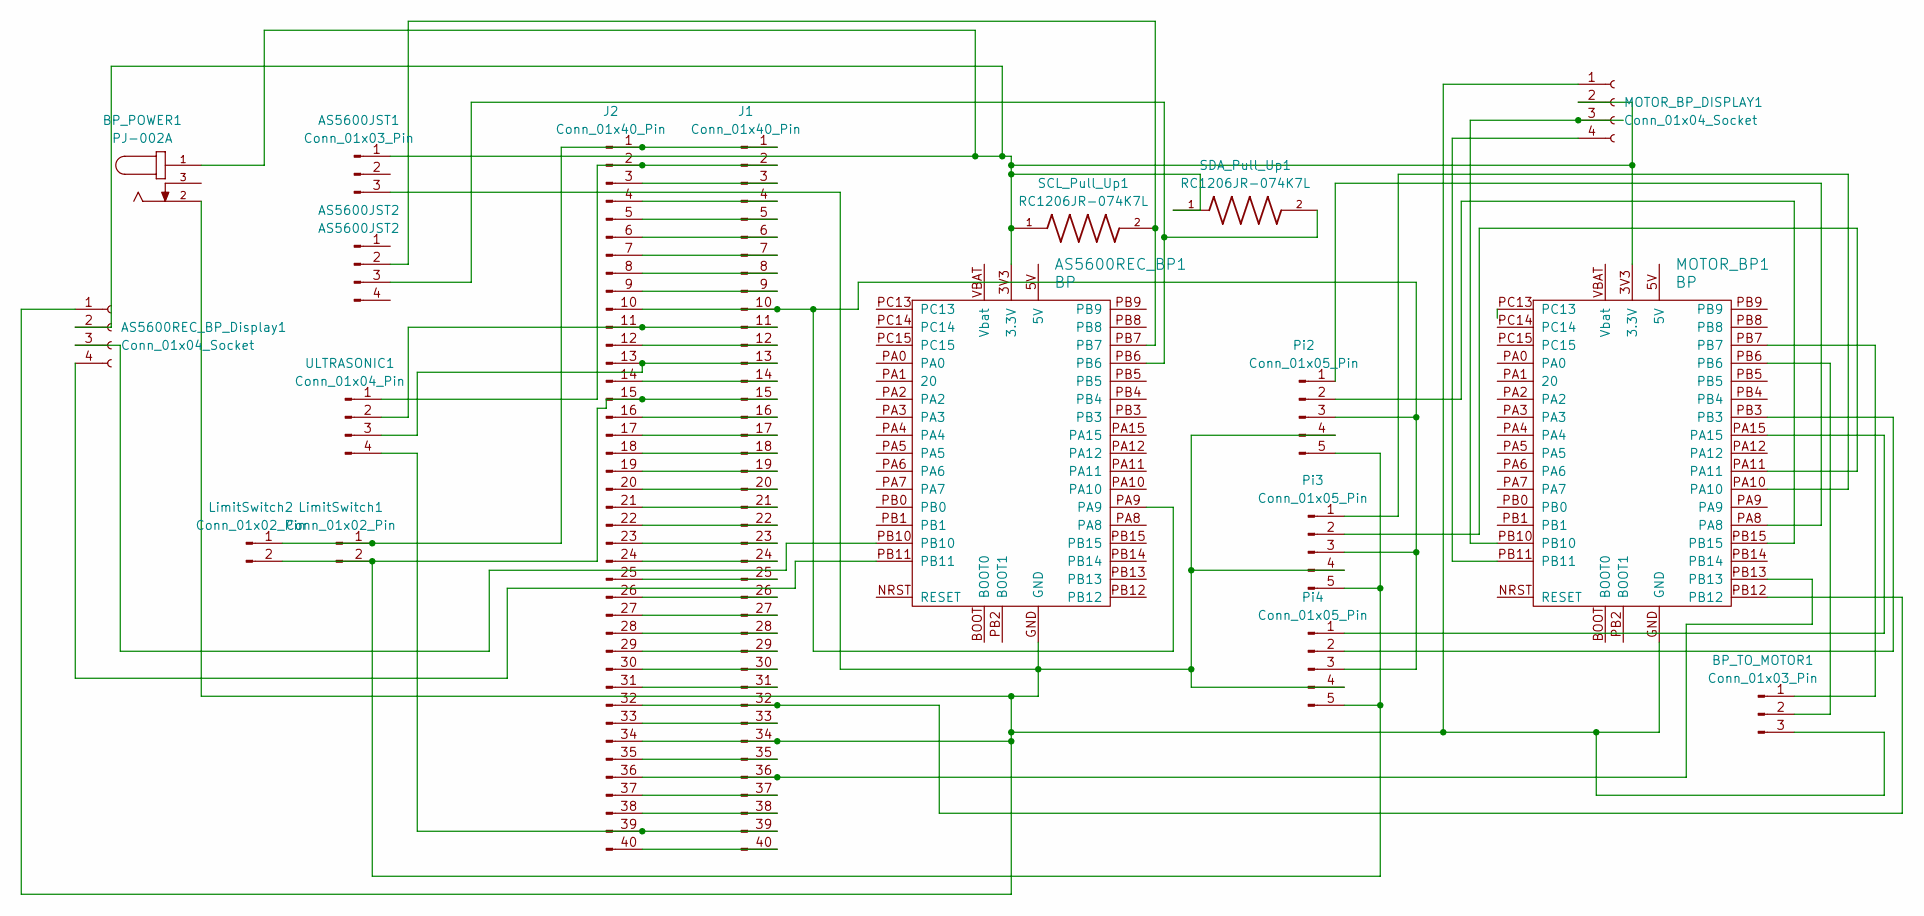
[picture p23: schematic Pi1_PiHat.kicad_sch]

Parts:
AS5600JST1: Conn_01x03_Pin; JST_EH_B3B-EH-A_1x03_P2.50mm_Vertical
AS5600JST2: AS5600JST2; JST_EH_B4B-EH-A_1x04_P2.50mm_Vertical
AS5600REC_BP1: BP; DevBoard_STM32_Bluepill
AS5600REC_BP_Display1: Conn_01x04_Socket; PinSocket_1x04_P2.54mm_Vertical
BP_POWER1: PJ-002A; CUI_PJ-002A; DigiKey_Part_Number CP-002A-ND
BP_TO_MOTOR1: Conn_01x03_Pin; JST_EH_B3B-EH-A_1x03_P2.50mm_Vertical
J1, J2: Conn_01x40_Pin; TE_7-146256-0
LimitSwitch1, LimitSwitch2: Conn_01x02_Pin; JST_EH_B2B-EH-A_1x02_P2.50mm_Vertical
MOTOR_BP1: BP; DevBoard_STM32_Bluepill
MOTOR_BP_DISPLAY1: Conn_01x04_Socket; PinSocket_1x04_P2.54mm_Vertical
Pi2, Pi3, Pi4: Conn_01x05_Pin; JST_EH_B5B-EH-A_1x05_P2.50mm_Vertical
SCL_Pull_Up1: RC1206JR-074K7L; RESC3116X65N; DigiKey_Part_Number 311-4.7KERTR-ND
SDA_Pull_Up1: RC1206JR-074K7L; RESC3116X65N; DigiKey_Part_Number 311-4.7KERTR-ND
ULTRASONIC1: Conn_01x04_Pin; JST_EH_B4B-EH-A_1x04_P2.50mm_Vertical

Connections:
unnamed: AS5600JST1.1, AS5600REC_BP1.3V3 (3.3V), AS5600REC_BP_Display1.2, BP_POWER1.1, MOTOR_BP1.3V3 (3.3V), MOTOR_BP_DISPLAY1.2, SCL_Pull_Up1.1, SDA_Pull_Up1.1
unnamed: AS5600JST1.3, AS5600REC_BP1.GND, AS5600REC_BP_Display1.1, BP_POWER1.2, BP_TO_MOTOR1.3, J1.34, J2.34, MOTOR_BP1.GND, MOTOR_BP_DISPLAY1.1, Pi2.4, Pi3.4, Pi4.4
unnamed: AS5600JST2.2, AS5600REC_BP1.PB7, SCL_Pull_Up1.2
unnamed: AS5600JST2.3, AS5600REC_BP1.PB6, SDA_Pull_Up1.2
unnamed: AS5600REC_BP1.PB10, AS5600REC_BP_Display1.3
unnamed: AS5600REC_BP1.PB11, AS5600REC_BP_Display1.4
unnamed: BP_TO_MOTOR1.1, MOTOR_BP1.PB7
unnamed: BP_TO_MOTOR1.2, MOTOR_BP1.PB6
unnamed: J1.1, J2.1, LimitSwitch1.1, LimitSwitch2.1
unnamed: J1.2, J2.2, ULTRASONIC1.1
unnamed: J1.3, J2.3
unnamed: J1.4, J2.4
unnamed: J1.5, J2.5
unnamed: J1.6, J2.6
unnamed: J1.7, J2.7
unnamed: J1.8, J2.8
unnamed: J1.9, J2.9
unnamed: AS5600REC_BP1.PA9, J1.10, J2.10, Pi2.3, Pi3.3, Pi4.3
unnamed: J1.11, J2.11, ULTRASONIC1.2
unnamed: J1.12, J2.12
unnamed: J1.13, J2.13, ULTRASONIC1.3
unnamed: J1.14, J2.14
unnamed: J1.15, J2.15, LimitSwitch1.2, LimitSwitch2.2, Pi2.5, Pi3.5, Pi4.5
unnamed: J1.16, J2.16
unnamed: J1.17, J2.17
unnamed: J1.18, J2.18
unnamed: J1.19, J2.19
unnamed: J1.20, J2.20
unnamed: J1.21, J2.21
unnamed: J1.22, J2.22
unnamed: J1.23, J2.23
unnamed: J1.24, J2.24
unnamed: J1.25, J2.25
unnamed: J1.26, J2.26
unnamed: J1.27, J2.27
unnamed: J1.28, J2.28
unnamed: J1.29, J2.29
unnamed: J1.30, J2.30
unnamed: J1.31, J2.31
unnamed: J1.32, J2.32, MOTOR_BP1.PB12
unnamed: J1.33, J2.33
unnamed: J1.35, J2.35
unnamed: J1.36, J2.36, MOTOR_BP1.PB13
unnamed: J1.37, J2.37
unnamed: J1.38, J2.38
unnamed: J1.39, J2.39, ULTRASONIC1.4
unnamed: J1.40, J2.40
unnamed: MOTOR_BP1.PB10, MOTOR_BP_DISPLAY1.3
unnamed: MOTOR_BP1.PB11, MOTOR_BP_DISPLAY1.4
unnamed: MOTOR_BP1.PA8, Pi2.1
unnamed: MOTOR_BP1.PB15, Pi2.2
unnamed: MOTOR_BP1.PA10, Pi3.1
unnamed: MOTOR_BP1.PA11, Pi3.2
unnamed: MOTOR_BP1.PA15, Pi4.1
unnamed: MOTOR_BP1.PB3, Pi4.2

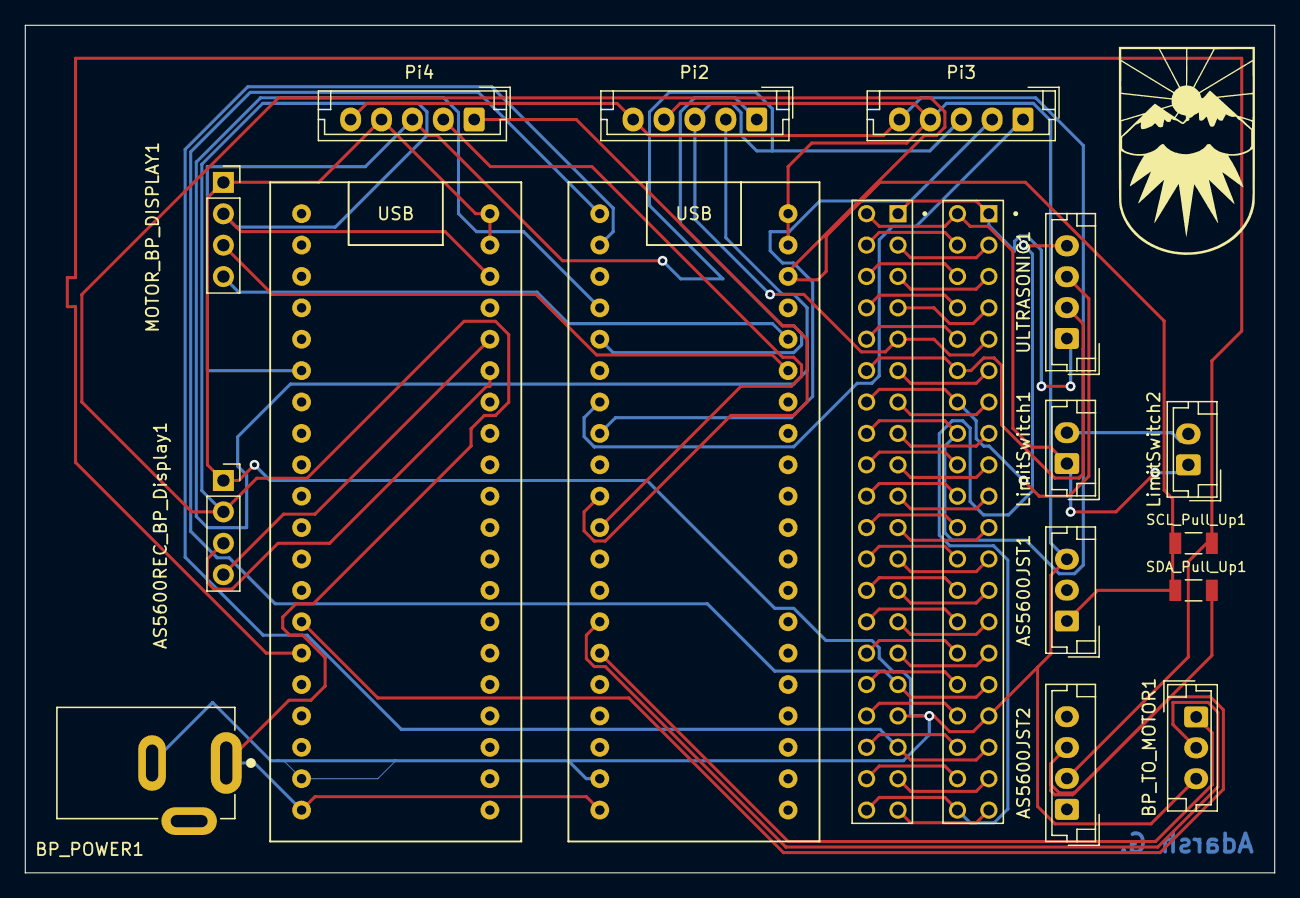
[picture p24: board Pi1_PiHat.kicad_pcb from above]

Board: 2 copper layers, 101.1 x 68.6 mm, 18 parts (0 on the bottom side), 55 nets.

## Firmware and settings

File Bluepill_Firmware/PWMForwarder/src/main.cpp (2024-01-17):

#include <Wire.h>
#include <Adafruit_SSD1306.h>
#include <vector>

#define SCREEN_WIDTH 128 // OLED display width, in pixels
#define SCREEN_HEIGHT 64 // OLED display height, in pixels
#define OLED_RESET 	-1 // This display does not have a reset pin accessible

#define PI1_PWM PB12
#define PI2_PWM PA8
#define PI3_PWM PA10
#define PI4_PWM PB3

#define PI1_DIR PB13
#define PI2_DIR PB15
#define PI3_DIR PA11
#define PI4_DIR PA15
    
#define PWM_OUT PB_6
#define DIR_OUT PB7

TwoWire Wire2(PB11, PB10);
Adafruit_SSD1306 display_handler(SCREEN_WIDTH, SCREEN_HEIGHT, &Wire2, OLED_RESET);
// Serial object to transmit to raspberry pis
int iterCount=0;
int pwmOutFreq=50000;
double piInputPeriod=5.0;
bool emptyVec=0;
long pulseTime1=0;
long pulseTime2=0;
long pulseTime3=0;
long pulseTime4=0;
int dir1=0;
int dir2=0;
int dir3=0;
int dir4=0;
long medianPulseTime=0;
long outputDutyCycle=0;
int dir=0;


void setup_display(Adafruit_SSD1306 &display_handler){
    display_handler.begin(SSD1306_SWITCHCAPVCC, 0x3C);
    // Displays Adafruit logo by default. call clearDisplay immediately if you don't want this.
    display_handler.display();
    delay(2000);

    // Displays "Hello world!" on the screen
    display_handler.clearDisplay();
    display_handler.setTextSize(1);
    display_handler.setTextColor(SSD1306_WHITE);
    display_handler.setCursor(0,0);
    display_handler.println("Hello world!");
    display_handler.display();
}

void initialize_pins(){
    pinMode(PI1_PWM, INPUT);
    pinMode(PI2_PWM, INPUT);
    pinMode(PI3_PWM, INPUT);
    pinMode(PI4_PWM, INPUT);

    pinMode(PI1_DIR, INPUT);
    pinMode(PI2_DIR, INPUT);
    pinMode(PI3_DIR, INPUT);
    pinMode(PI4_DIR, INPUT);

    pinMode(PWM_OUT, OUTPUT);
    pinMode(DIR_OUT, OUTPUT);
    pwm_start(PWM_OUT, pwmOutFreq, 0, TimerCompareFormat_t::RESOLUTION_12B_COMPARE_FORMAT);
}

void read_pi_inputs(){
    pulseTime1=pulseIn(PI1_PWM, HIGH, 1000);//(pow(10,7));
    pulseTime2=pulseIn(PI2_PWM, HIGH, 1000);//(pow(10,7));
    pulseTime3=pulseIn(PI3_PWM, HIGH, 1000);//(pow(10,7));
    pulseTime4=pulseIn(PI4_PWM, HIGH, 1000);//(pow(10,7));

    dir1=digitalRead(PI1_DIR);
    dir2=digitalRead(PI2_DIR);
    dir3=digitalRead(PI3_DIR);
    dir4=digitalRead(PI4_DIR);
}

void compute_median(){
    // create vector of pulse times if pulse time is not 0
    std::vector<long> pulseTimes;
    // if dir1 is high, give pulseTime1 a negative sign 
    if(pulseTime1) {if(dir1) pulseTime1=-pulseTime1; pulseTimes.push_back(pulseTime1);};
    if(pulseTime2) {if(dir2) pulseTime2=-pulseTime2; pulseTimes.push_back(pulseTime2);};
    if(pulseTime3) {if(dir3) pulseTime3=-pulseTime3; pulseTimes.push_back(pulseTime3);};
    if(pulseTime4) {if(dir4) pulseTime4=-pulseTime4; pulseTimes.push_back(pulseTime4);};
    

    // find median of pulse times
    if(!pulseTimes.size()){
        display_handler.clearDisplay();
        display_handler.setCursor(0,0);
        emptyVec=!emptyVec;
        display_handler.println("Empty Vector: " + String(emptyVec));
        display_handler.display();
    } else{
        std::sort(pulseTimes.begin(), pulseTimes.end());
        long range=abs(pulseTimes[pulseTimes.size()-1]-pulseTimes[0]);
        std::sort(pulseTimes.begin(), pulseTimes.end());
        medianPulseTime=double(pulseTimes[pulseTimes.size()/2]);
        outputDutyCycle=abs(double(medianPulseTime))/piInputPeriod;
        dir=medianPulseTime<0;
        display_handler.clearDisplay();
        display_handler.setCursor(0,0);
        display_handler.println("size: " + String(pulseTimes.size()));
        display_handler.println("Med D.C: " + String(abs(double(outputDutyCycle))));
        display_handler.println("pulseTimes[0] :" + String(double(pulseTimes[0])));
        display_handler.println("Med: " + String(double(medianPulseTime)));
        display_handler.println("Pi1 P.T: " + String(pulseTime1));
        display_handler.println("Pi1 Dut: " + String(double(pulseTime1)/piInputPeriod));
        display_handler.println("Range: " + String(range));
        display_handler.println("Direction: " + String(dir));
        display_handler.display();
    }
}

void output_to_motor_driver(){
    pwm_start(PWM_OUT, pwmOutFreq, outputDutyCycle, TimerCompareFormat_t::PERCENT_COMPARE_FORMAT);
    digitalWrite(DIR_OUT, dir);
}

// ARDUINO SETUP LOOP
void setup() {
    setup_display(display_handler);
    initialize_pins();
}


// ARDUINO MAIN LOOP
void loop() {
    unsigned long outputDutyCycle=0;
    int dir=0;

    read_pi_inputs();

    compute_median();
    // outputs previously computed median to the motor driver
    output_to_motor_driver();
    // display_handler.clearDisplay();
    // display_handler.setCursor(0,0);
    // display_handler.println("Itercount: " + String(iterCount++));
    // // // display_handler.println("Pulse time: " + String(pulseTime));
    // display_handler.println("Duty cycle: " + String(outputDutyCycle));
    // display_handler.println("Direction: " + String(dir));
    // // // display_handler.println("Pi number: " + String(piNum));
    // display_handler.display();
    // display_handler.clearDisplay();
};

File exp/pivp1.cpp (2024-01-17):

#include "achal/bft_kvs.h"
#include "achal/eig_tree.h"
#include "applications/physical_ivp.h"
#include "common.h"
#include "utils/logging.h"
#include "utils/macros.h"
#include "utils/misc.h"
#include <cstdlib>
#include <fstream>
#include <iostream>
#include <json/json.h>
#include <pigpio.h>
#include <stdlib.h>

#define BFT_KVS_DEFAULT_NUM_ROUNDS 1
#define BFT_KVS_DEFAULT_NETWORK_DELAY_US 100
#define BFT_KVS_DEFAULT_PRIORITY 2
#define BFT_KVS_TASK_ID(NODE_ID, CPU_ID) ((1000 * NODE_ID) + (100 * CPU_ID))

log4cpp::Category *logger;

static uint8_t faulty_data[sizeof(struct Achal::eig_node<100, 7, 15>) * 100];

// GPIO pin defs
int motor_pin = 12, dir_pin = 16, us_trig = 17, us_echo = 27, lim_sw = 22;

// IDK WHAT THIS IS FOR
int get_period_based_priority(uint64_t period_ms) {
  if (period_ms <= 1) {
    return 26;
  } else if (period_ms <= 2) {
    return 24;
  } else if (period_ms <= 5) {
    return 23;
  } else if (period_ms <= 10) {
    return 22;
  } else if (period_ms <= 20) {
    return 21;
  } else if (period_ms <= 50) {
    return 20;
  } else if (period_ms <= 100) {
    return 19;
  } else if (period_ms <= 200) {
    return 18;
  }

  return 17;
}

int limit_switch = 22;
Applications::PositionTask *periodic_task;
bool runProgram = true;

void limitSwitchISR(int gpio, int level, uint32_t tick) {
  std::cout << "ISR ENTERED" << std::endl;
  this_thread::sleep_for(50ms);
  if (gpioRead(limit_switch)) {
    periodic_task->stop_flag = true;
  }
}

void pwm_output_test() {
  gpioSetMode(motor_pin, PI_OUTPUT);
  gpioSetMode(dir_pin, PI_OUTPUT);
  gpioSetPWMfrequency(motor_pin, 2000);
  while (true) {
    for (int i = 1; i < 20; i++) {
      std::cout << "PWM Duty Cycle: " << i * 10 << " out of 255" << std::endl;
      gpioPWM(motor_pin, i * 10);
      this_thread::sleep_for(5000ms);
    }
  }
}


int main(int argc, char **argv) {
  gpioTerminate();
  gpioInitialise();
  // limit_sw_test();
  // ultrasonic_test();
  // AS5600_test();
  // pwm_output_test();

  int node_id = std::stoi(argv[1]);
  int total_nodes = std::stoi(argv[2]);
  uint64_t period_ms = std::stoi(argv[3]);
  uint64_t ang_period_ms = std::stoi(argv[4]);
  double pos_Kp = std::stod(argv[5]);
  double pos_Kd = std::stod(argv[6]);
  double pos_Ki = std::stod(argv[7]);
  double ang_Kp = std::stod(argv[8]);
  double ang_Kd = std::stod(argv[9]);
  double ang_Ki = std::stod(argv[10]);
  double position_set_point;
  uint16_t angle_set_point;

  std::memset((void *)faulty_data, 3, sizeof(faulty_data));

  log4cpp::Category *logger;
  std::string def_log_file = "Pi" + std::to_string(node_id) + "_log.log";
  if (std::remove(def_log_file.c_str()) == 0) {
    std::cout << "Existing log file deleted successfully." << std::endl;
  } else {
    // Check if the file doesn't exist (errno == ENOENT)
    if (errno != ENOENT) {
      std::cerr << "Error deleting existing log file." << std::endl;
      return 1;
    }
  }

  bool logger_stats = Utils::get_new_logger(
      "PIvP", def_log_file, log4cpp::Priority::PriorityLevel::DEBUG, &logger);
  // if (gpioInitialise() < 0) {
  //   logger << "pigpio initialization failed, code " << std::to_string(gpioInitialise());
  //   return -1;
  // }

  // Use this to log to terminal
  // bool logger_stats = Utils::get_new_logger(
  //     "PIvP", log4cpp::Priority::PriorityLevel::DEBUG, &logger);

  Json::Value calibration;
  std::ifstream calibrationFile("exp/calibration.json");
  Json::CharReaderBuilder reader;
  JSONCPP_STRING errs;
  Json::parseFromStream(reader, calibrationFile, &calibration, &errs);
  calibrationFile.close();

  if (errs.empty()) {
    if (argc > 11)
      position_set_point = std::stod(argv[11]);
    else
      position_set_point = calibration["Position Set Point"].asDouble();

    if (argc > 12)
      angle_set_point = stoi(argv[12]);
    else
      angle_set_point = calibration["Angle Set Point"].asInt();
  }

  calibration["Position Set Point"] = position_set_point;
  calibration["Angle Set Point"] = angle_set_point;

  Json::StreamWriterBuilder writer;
  std::ofstream calibrationFileOut("exp/calibration.json");
  calibrationFileOut << Json::writeString(writer, calibration);
  calibrationFileOut.close();
  std::cout << "Configuration updated in calibration.json" << std::endl;

  std::string kvs_type = "BFTKVS";
  std::string output_file_name = "out_file";
  int cpus_used = 1;
  int num_tasks_per_cpu = 1;
  int fault_mode;
  int number_of_faulty_node;
  int num_nmr_instances = 1;
  uint64_t pivp_task_wcet_ms = 6;
  int exp_duration_s = 10000;
  int replication_factor = total_nodes;

  gpioInitialise();
  gpioSetMode(limit_switch, PI_INPUT);
  gpioSetPullUpDown(limit_switch, PI_PUD_DOWN);
  gpioSetISRFunc(limit_switch, RISING_EDGE, 0, limitSwitchISR);
  std::vector<Achal::KVSInterface *> kvs_instances;

  if (total_nodes < 2) {
    std::cout << "single node setup" << std::endl;
    Achal::config_t simple_kvs_config;
    simple_kvs_config.id = BFT_KVS_TASK_ID(node_id, 0);
    simple_kvs_config.cpu = 0;
    simple_kvs_config.period_ns = MS_TO_NS(period_ms);
    uint64_t nmr_specific_offset_ns =
        0 * (MS_TO_NS(period_ms) / num_nmr_instances);
    simple_kvs_config.offset_ns =
        nmr_specific_offset_ns +
        MS_TO_NS((num_tasks_per_cpu * pivp_task_wcet_ms));
    simple_kvs_config.logger = logger;
    simple_kvs_config.max_network_delay_ns =
        US_TO_NS(BFT_KVS_DEFAULT_NETWORK_DELAY_US);
    simple_kvs_config.max_rounds = BFT_KVS_DEFAULT_NUM_ROUNDS;
    simple_kvs_config.max_jobs =
        SEC_TO_NS(exp_duration_s) / simple_kvs_config.period_ns;
    simple_kvs_config.priority = BFT_KVS_DEFAULT_PRIORITY;

    auto temp = new Achal::SimpleKVS(simple_kvs_config);

    kvs_instances.push_back(temp);
  } else {
    std::cout << "multinode setup" << std::endl;
    std::vector<Achal::config_t> bft_kvs_configs;
    for (unsigned nmr_id = 0; nmr_id < num_nmr_instances; nmr_id++) {
      Achal::config_t bft_kvs_config;
      bft_kvs_config.period_ns = MS_TO_NS(period_ms);
      bft_kvs_config.priority = BFT_KVS_DEFAULT_PRIORITY;
      uint64_t nmr_specific_offset_ns =
          nmr_id * (MS_TO_NS(period_ms) / num_nmr_instances);
      bft_kvs_config.offset_ns =
          nmr_specific_offset_ns +
          MS_TO_NS((num_tasks_per_cpu * pivp_task_wcet_ms));
      bft_kvs_config.logger = logger;
      bft_kvs_config.max_network_delay_ns =
          US_TO_NS(BFT_KVS_DEFAULT_NETWORK_DELAY_US);
      bft_kvs_config.max_rounds = BFT_KVS_DEFAULT_NUM_ROUNDS;
      bft_kvs_config.max_jobs =
          SEC_TO_NS(exp_duration_s) / bft_kvs_config.period_ns;
      bft_kvs_config.max_failed_comms = 80;
      bft_kvs_config.failure_time_multiple = 100;
      bft_kvs_config.wcet_kvs = 0;
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

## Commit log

2022-11-28 Porting Achal from our private repo
    [default.cfg, kzh15.cfg, kzh15_100pcu_924l.cfg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]
2024-01-17 initial public commit
    [AS5600_Mount.stl, Cart_Timing_Belt_Mount.stl, Idler_Mount.stl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]
